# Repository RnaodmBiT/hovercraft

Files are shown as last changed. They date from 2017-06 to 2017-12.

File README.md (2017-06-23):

 # MiniBot

This project will produce a PCB design that can be used for prototyping remote control vehicles. It is inspired by the University of Canterbury ECE Departments 'Wacky Racers' competition. The objective is to follow most of the rules of that competition however the entire design will fit on a single PCB and be as small as possible.

 ## Requirements
  - Support a number of external ESCs and Servos.
  - Be remote controlled. This might require a second USB dongle to be produced if Bluetooth or WiFi isn't used.
  - It should include an accelerometer, gyroscope, and magnetometer for any control systems.
  - Be programmable over SWD or USB.
  - Use as minimum number of parts.
  - Make use of an STM32 microcontroller.
  - Provide external PIO access for use in different projects.

 ## Connectivity
  - Radio
    - RN41
      - UART
      - LED connected to GPIO5 (Open Drain)
      - Connect GPIOs 3/4/6 to GND
      - Connect GPIO 7 to ground with solder bridge high

  - Accelerometer
    - LSM6DS3US
      - I2C

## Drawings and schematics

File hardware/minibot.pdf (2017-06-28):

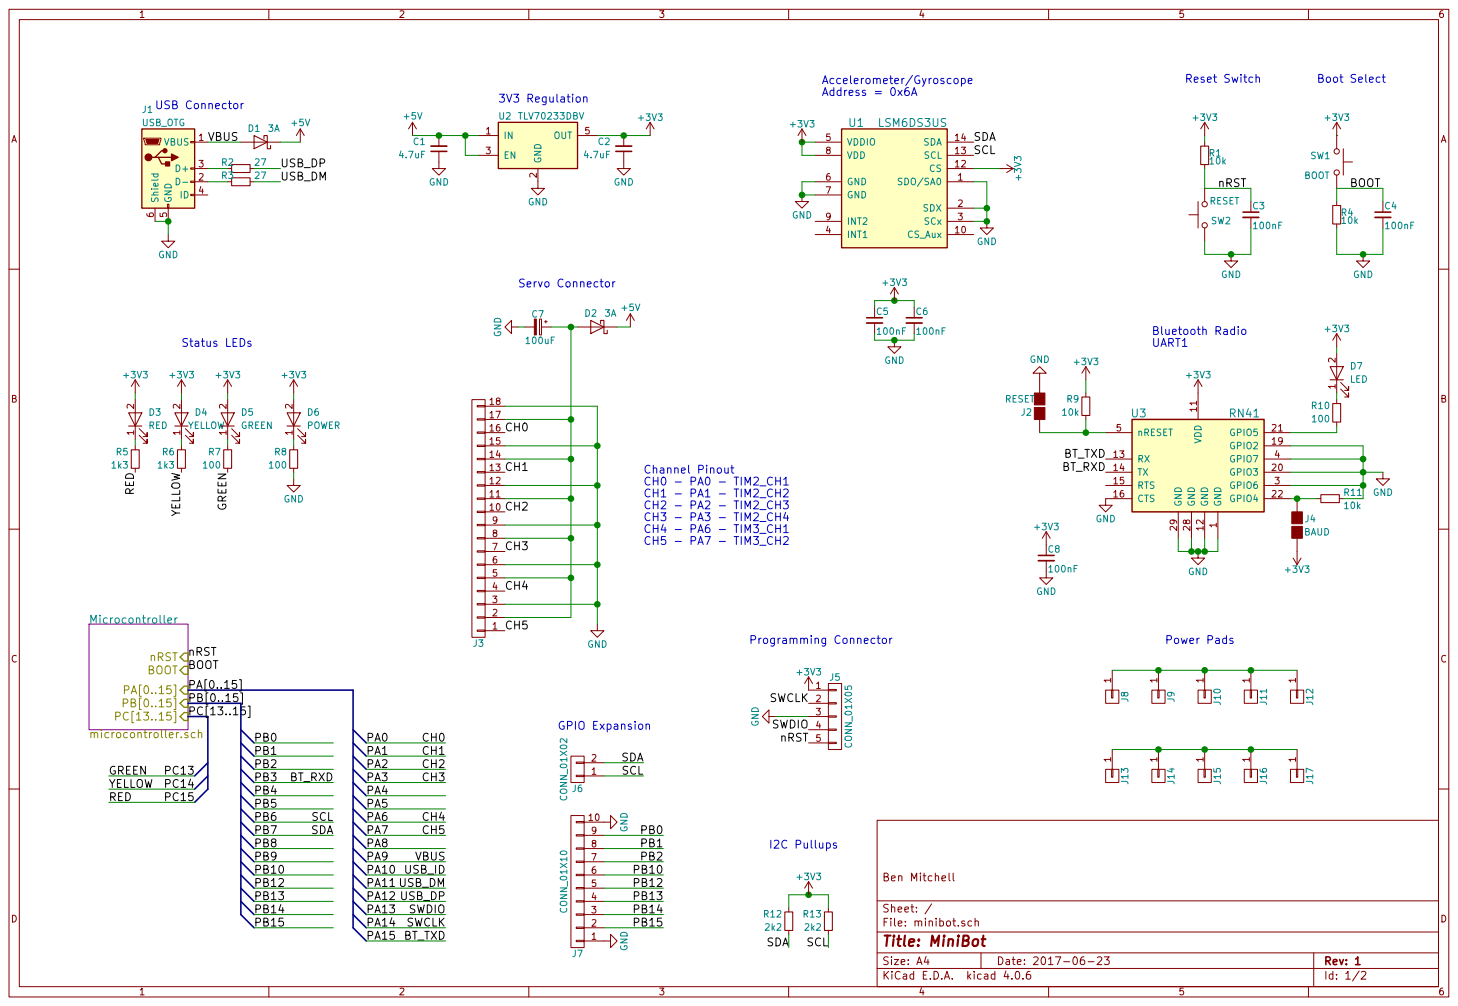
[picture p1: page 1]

17
CH0 15

14
CH1 12

11
CH2 9

CH3 6

CH4 3

Id: 1/2 Title: MiniBot File: minibot.sch Sheet: / Ben Mitchell Microcontroller microcontroller.sch

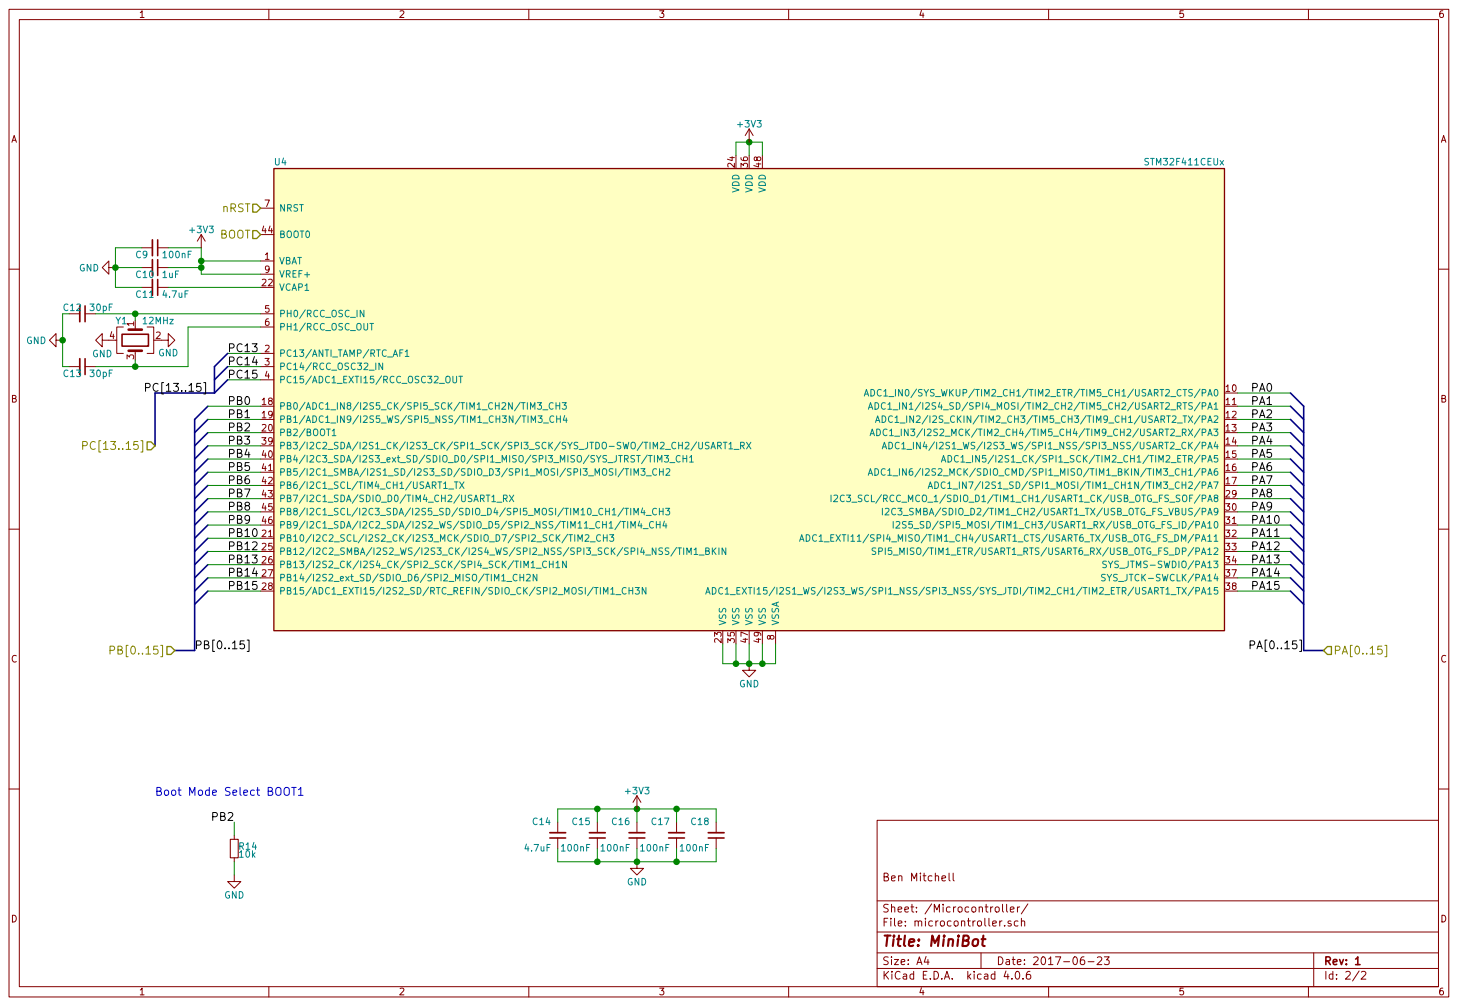
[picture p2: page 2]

Id: 2/2 Title: MiniBot File: microcontroller.sch Sheet: /Microcontroller/ Ben Mitchell

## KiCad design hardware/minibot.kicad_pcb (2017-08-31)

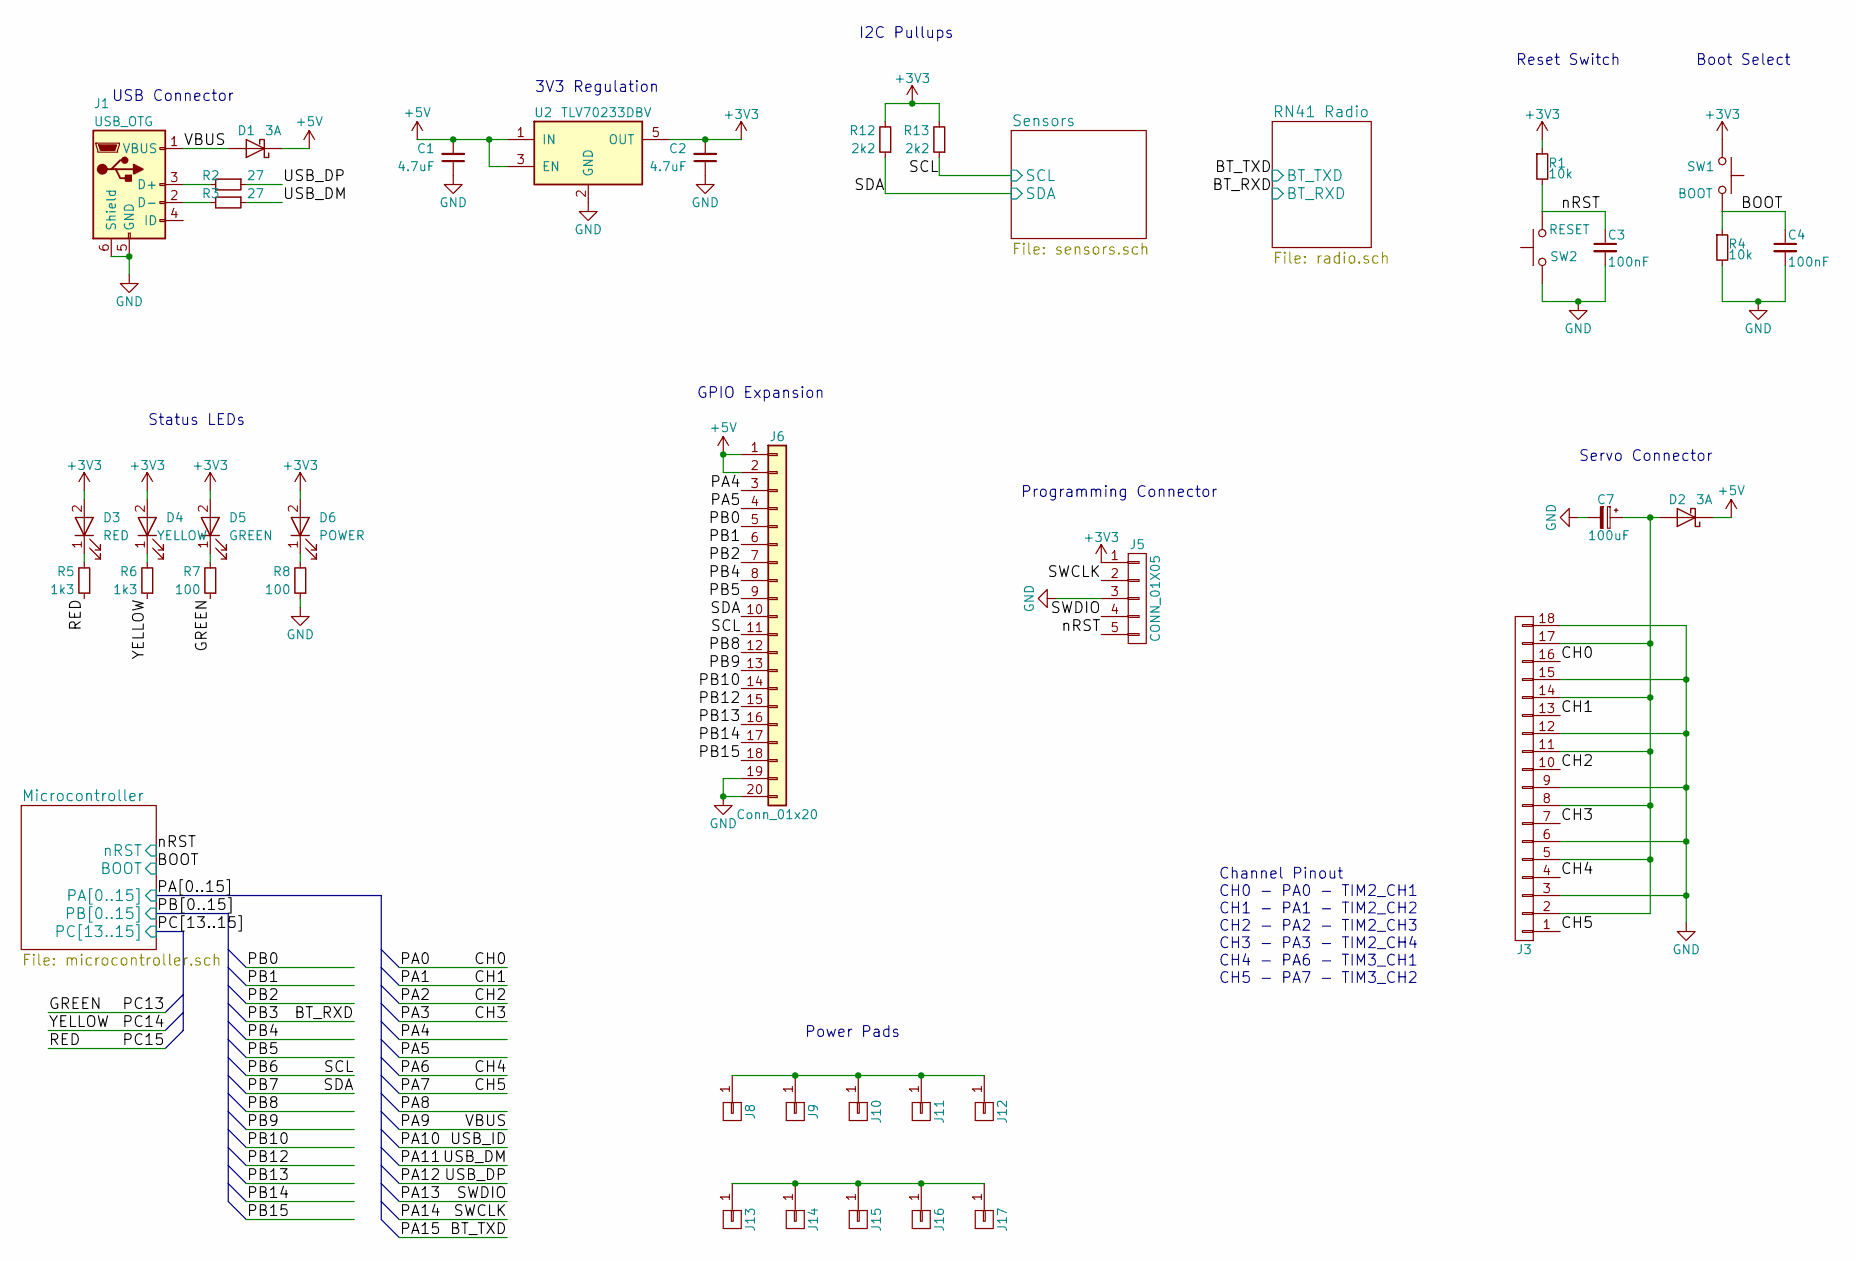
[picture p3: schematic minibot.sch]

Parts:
C1, C2: 4.7uF; C_0805
C3, C4: 100nF; C_0603
C7: 100uF; CP_Elec_6.3x5.3
D1, D2: 3A; D_SMA
D3: RED; LED_0603
D4: YELLOW; LED_0603
D5: GREEN; LED_0603
D6: POWER; LED_0603
J1: USB_OTG; USB_Micro-B
J3: CONN_01X18; Pin_Header_Angled_3x06_Pitch2.54mm
J5: CONN_01X05; Pin_Header_Straight_1x05_Pitch2.54mm
J6: Conn_01x20; IDC_Header_Straight_20pins
J8, J9, J10, J11, J12, J13, J14, J15, J16, J17: CONN_01X01; Pad
R1, R4: 10k; R_0603
R2, R3: 27; R_0603
R5, R6: 1k3; R_0603
R7, R8: 100; R_0603
R12, R13: 2k2; R_0603
SW1: BOOT; Panasonic_EVQPUK_EVQPUB
SW2: RESET; Panasonic_EVQPUK_EVQPUB
U2: TLV70233DBV; SOT-23-5

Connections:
+3V3: C2.2, D3.2 (A), D4.2 (A), D5.2 (A), D6.2 (A), J5.1, R1.1, R12.2, R13.2, SW1.1, U2.5 (OUT); also elsewhere on the board
+5V: C1.2, D1.1 (K), D2.1 (K), J6.1, J6.2, U2.1 (IN), U2.3 (EN)
/BOOT: C4.1, R4.1, SW1.2; also elsewhere on the board
/CH0: J3.16; also elsewhere on the board
/CH1: J3.13; also elsewhere on the board
/CH2: J3.10; also elsewhere on the board
/CH3: J3.7; also elsewhere on the board
/CH4: J3.4; also elsewhere on the board
/CH5: J3.1; also elsewhere on the board
/GREEN: R7.1; also elsewhere on the board
/PA4: J6.3; also elsewhere on the board
/PA5: J6.4; also elsewhere on the board
/PA9: D1.2 (A), J1.1 (VBUS); also elsewhere on the board
/PA11: R3.1; also elsewhere on the board
/PA12: R2.1; also elsewhere on the board
/PA13: J5.4; also elsewhere on the board
/PA14: J5.2; also elsewhere on the board
/PB0: J6.5; also elsewhere on the board
/PB1: J6.6; also elsewhere on the board
/PB2: J6.7; also elsewhere on the board
/PB4: J6.8; also elsewhere on the board
/PB5: J6.9; also elsewhere on the board
/PB6: J6.11, R13.1; also elsewhere on the board
/PB7: J6.10, R12.1; also elsewhere on the board
/PB8: J6.12; also elsewhere on the board
/PB9: J6.13; also elsewhere on the board
/PB10: J6.14; also elsewhere on the board
/PB12: J6.15; also elsewhere on the board
/PB13: J6.16; also elsewhere on the board
/PB14: J6.17; also elsewhere on the board
/PB15: J6.18; also elsewhere on the board
/PC14: R6.1; also elsewhere on the board
/PC15: R5.1; also elsewhere on the board
/nRST: C3.1, J5.5, R1.2, SW2.2; also elsewhere on the board
GND: C1.1, C2.1, C3.2, C4.2, C7.2, J1.5 (GND), J1.6 (Shield), J3.3, J3.6, J3.9, J3.12, J3.15, J3.18, J5.3, J6.19, J6.20, R4.2, R8.1, SW2.1, U2.2 (GND); also elsewhere on the board
unnamed: C7.1, D2.2 (A), J3.2, J3.5, J3.8, J3.11, J3.14, J3.17
unnamed: D3.1 (K), R5.2
unnamed: D4.1 (K), R6.2
unnamed: D5.1 (K), R7.2
unnamed: D6.1 (K), R8.2
unnamed: J1.2 (D-), R3.2
unnamed: J1.3 (D+), R2.2
unnamed: J8.1, J9.1, J10.1, J11.1, J12.1
unnamed: J13.1, J14.1, J15.1, J16.1, J17.1

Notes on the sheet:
Reset Switch
Boot Select
Servo Connector
USB Connector
3V3 Regulation
Status LEDs
Programming Connector
I2C Pullups
Channel Pinout CH0 - PA0 - TIM2_CH1 CH1 - PA1 - TIM2_CH2 CH2 - PA2 - TIM2_CH3 CH3 - PA3 - TIM2_CH4 CH4 - PA6 - TIM3_CH1 CH5 - PA7 - TIM3_CH2
GPIO Expansion
Power Pads

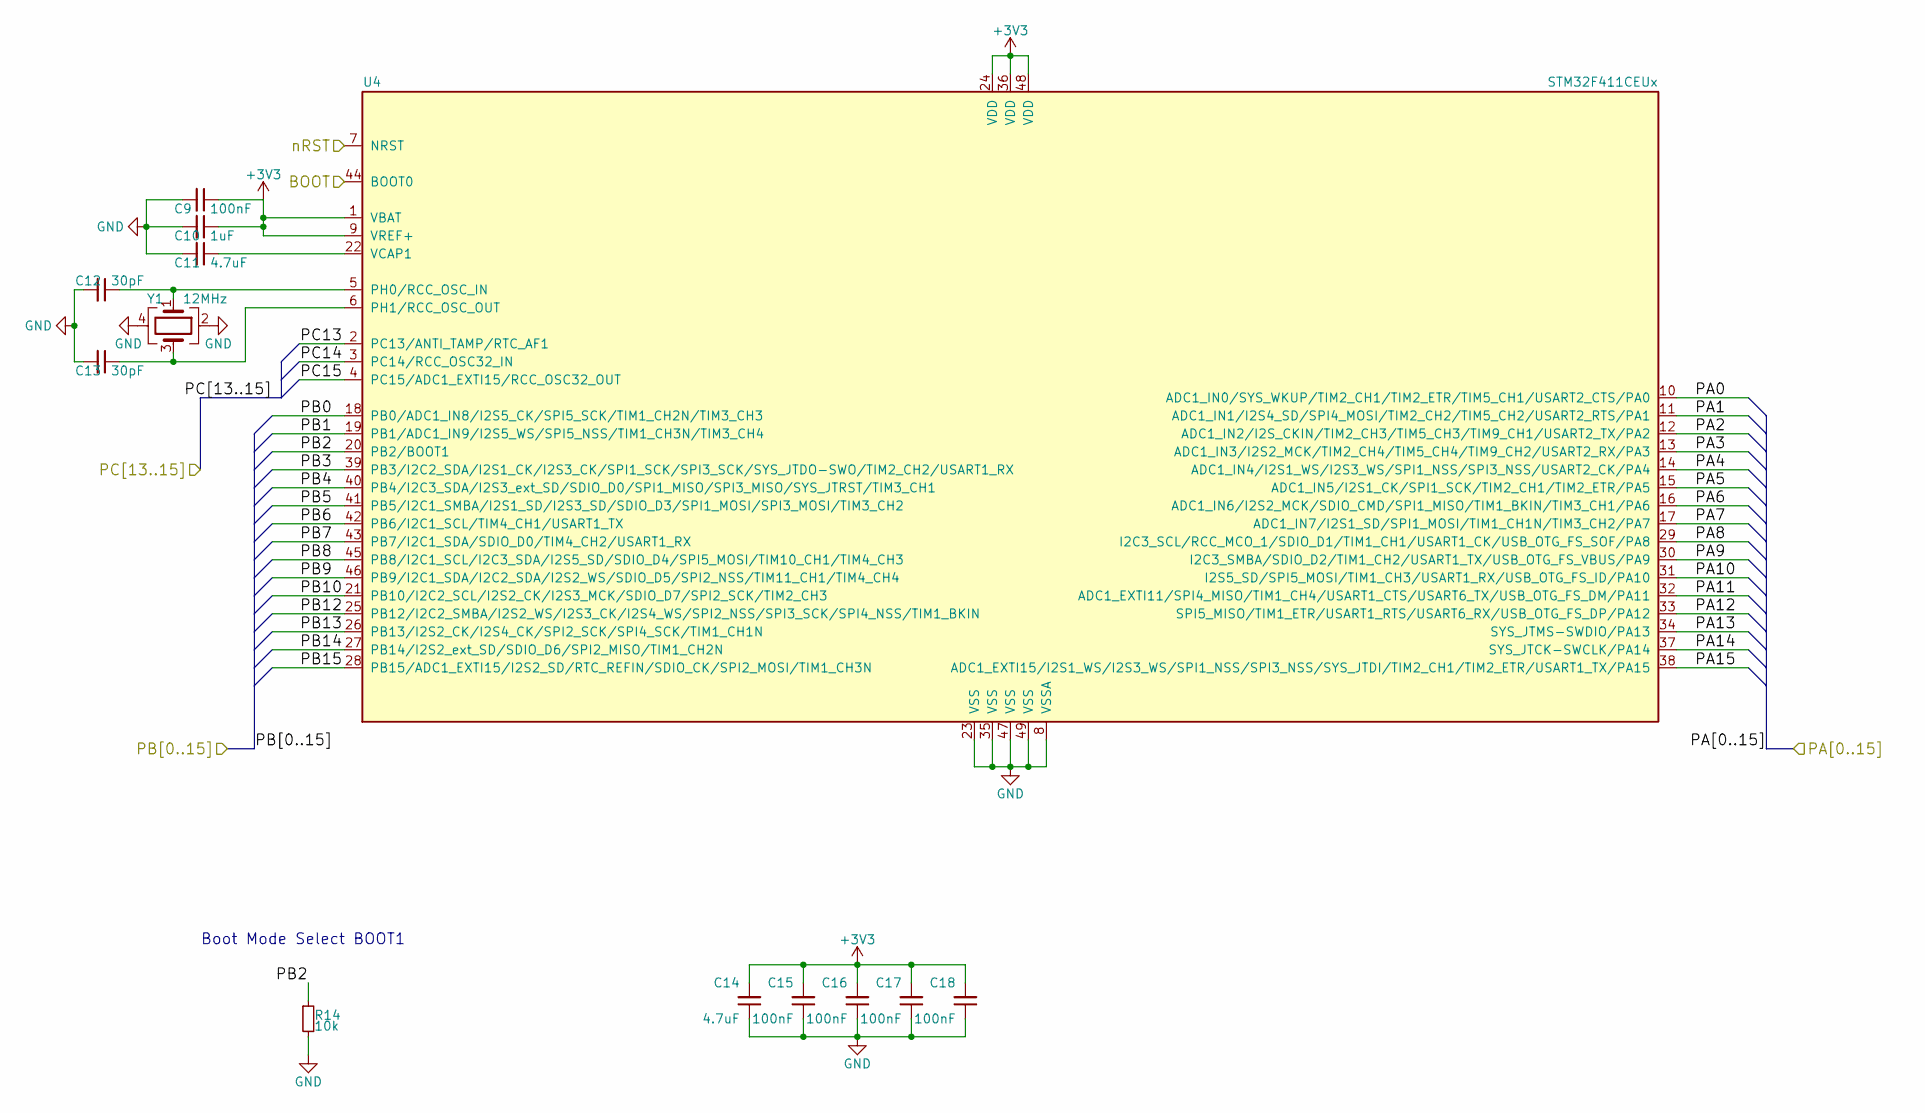
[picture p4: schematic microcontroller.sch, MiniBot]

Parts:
C9, C15, C16, C17, C18: 100nF; C_0603
C10: 1uF; C_0805
C11, C14: 4.7uF; C_0805
C12, C13: 30pF; C_0402
R14: 10k; R_0603
U4: STM32F411CEUx; TQFP-48_7x7mm_Pitch0.5mm
Y1: 12MHz; Crystal_SMD_3225-4pin_3.2x2.5mm

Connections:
+3V3: C9.1, C10.1, C14.2, C15.2, C16.2, C17.2, C18.2, U4.1 (VBAT), U4.9 (VREF+), U4.24 (VDD), U4.36 (VDD), U4.48 (VDD); also elsewhere on the board
/BOOT: U4.44 (BOOT0); also elsewhere on the board
/BT_RXD: U4.39 (PB3/I2C2_SDA/I2S1_CK/I2S3_CK/SPI1_SCK/S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); also elsewhere on the board
/BT_TXD: U4.38 (ADC1_EXTI15/I2S1_WS/I2S3_WS/SPI1_NSS/SP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); also elsewhere on the board
/CH0: U4.10 (ADC1_IN0/SYS_WKUP/TIM2_CH1/TIM2_ETR/TIM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); also elsewhere on the board
/CH1: U4.11 (ADC1_IN1/I2S4_SD/SPI4_MOSI/TIM2_CH2/TIM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); also elsewhere on the board
/CH2: U4.12 (ADC1_IN2/I2S_CKIN/TIM2_CH3/TIM5_CH3/TIM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); also elsewhere on the board
/CH3: U4.13 (ADC1_IN3/I2S2_MCK/TIM2_CH4/TIM5_CH4/TIM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); also elsewhere on the board
/CH4: U4.16 (ADC1_IN6/I2S2_MCK/SDIO_CMD/SPI1_MISO/TI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); also elsewhere on the board
/CH5: U4.17 (ADC1_IN7/I2S1_SD/SPI1_MOSI/TIM1_CH1N/TI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); also elsewhere on the board
/GREEN: U4.2 (PC13/ANTI_TAMP/RTC_AF1); also elsewhere on the board
/PA4: U4.14 (ADC1_IN4/I2S1_WS/I2S3_WS/SPI1_NSS/SPI3_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); also elsewhere on the board
/PA5: U4.15 (ADC1_IN5/I2S1_CK/SPI1_SCK/TIM2_CH1/TIM2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); also elsewhere on the board
/PA8: U4.29 (I2C3_SCL/RCC_MCO_1/SDIO_D1/TIM1_CH1/USA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)
/PA9: U4.30 (I2C3_SMBA/SDIO_D2/TIM1_CH2/USART1_TX/US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); also elsewhere on the board
/PA10: U4.31 (I2S5_SD/SPI5_MOSI/TIM1_CH3/USART1_RX/US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)
/PA11: U4.32 (ADC1_EXTI11/SPI4_MISO/TIM1_CH4/USART1_C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); also elsewhere on the board
/PA12: U4.33 (SPI5_MISO/TIM1_ETR/USART1_RTS/USART6_RX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); also elsewhere on the board
/PA13: U4.34 (SYS_JTMS-SWDIO/PA13); also elsewhere on the board
/PA14: U4.37 (SYS_JTCK-SWCLK/PA14); also elsewhere on the board
/PB0: U4.18 (PB0/ADC1_IN8/I2S5_CK/SPI5_SCK/TIM1_CH2N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); also elsewhere on the board
/PB1: U4.19 (PB1/ADC1_IN9/I2S5_WS/SPI5_NSS/TIM1_CH3N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); also elsewhere on the board
/PB2: R14.1, U4.20 (PB2/BOOT1); also elsewhere on the board
/PB4: U4.40 (PB4/I2C3_SDA/I2S3_ext_SD/SDIO_D0/SPI1_M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); also elsewhere on the board
/PB5: U4.41 (PB5/I2C1_SMBA/I2S1_SD/I2S3_SD/SDIO_D3/S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); also elsewhere on the board
/PB6: U4.42 (PB6/I2C1_SCL/TIM4_CH1/USART1_TX); also elsewhere on the board
/PB7: U4.43 (PB7/I2C1_SDA/SDIO_D0/TIM4_CH2/USART1_RX); also elsewhere on the board
/PB8: U4.45 (PB8/I2C1_SCL/I2C3_SDA/I2S5_SD/SDIO_D4/S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); also elsewhere on the board
/PB9: U4.46 (PB9/I2C1_SDA/I2C2_SDA/I2S2_WS/SDIO_D5/S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); also elsewhere on the board
/PB10: U4.21 (PB10/I2C2_SCL/I2S2_CK/I2S3_MCK/SDIO_D7/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); also elsewhere on the board
/PB12: U4.25 (PB12/I2C2_SMBA/I2S2_WS/I2S3_CK/I2S4_WS/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); also elsewhere on the board
/PB13: U4.26 (PB13/I2S2_CK/I2S4_CK/SPI2_SCK/SPI4_SCK/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); also elsewhere on the board
/PB14: U4.27 (PB14/I2S2_ext_SD/SDIO_D6/SPI2_MISO/TIM1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); also elsewhere on the board
/PB15: U4.28 (PB15/ADC1_EXTI15/I2S2_SD/RTC_REFIN/SDIO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); also elsewhere on the board
/PC14: U4.3 (PC14/RCC_OSC32_IN); also elsewhere on the board
/PC15: U4.4 (PC15/ADC1_EXTI15/RCC_OSC32_OUT); also elsewhere on the board
/nRST: U4.7 (NRST); also elsewhere on the board
GND: C9.2, C10.2, C11.2, C12.2, C13.2, C14.1, C15.1, C16.1, C17.1, C18.1, R14.2, U4.8 (VSSA), U4.23 (VSS), U4.35 (VSS), U4.47 (VSS), U4.49 (VSS), Y1.2, Y1.4; also elsewhere on the board
unnamed: C11.1, U4.22 (VCAP1)
unnamed: C12.1, U4.5 (PH0/RCC_OSC_IN), Y1.1
unnamed: C13.1, U4.6 (PH1/RCC_OSC_OUT), Y1.3

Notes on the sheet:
Boot Mode Select BOOT1

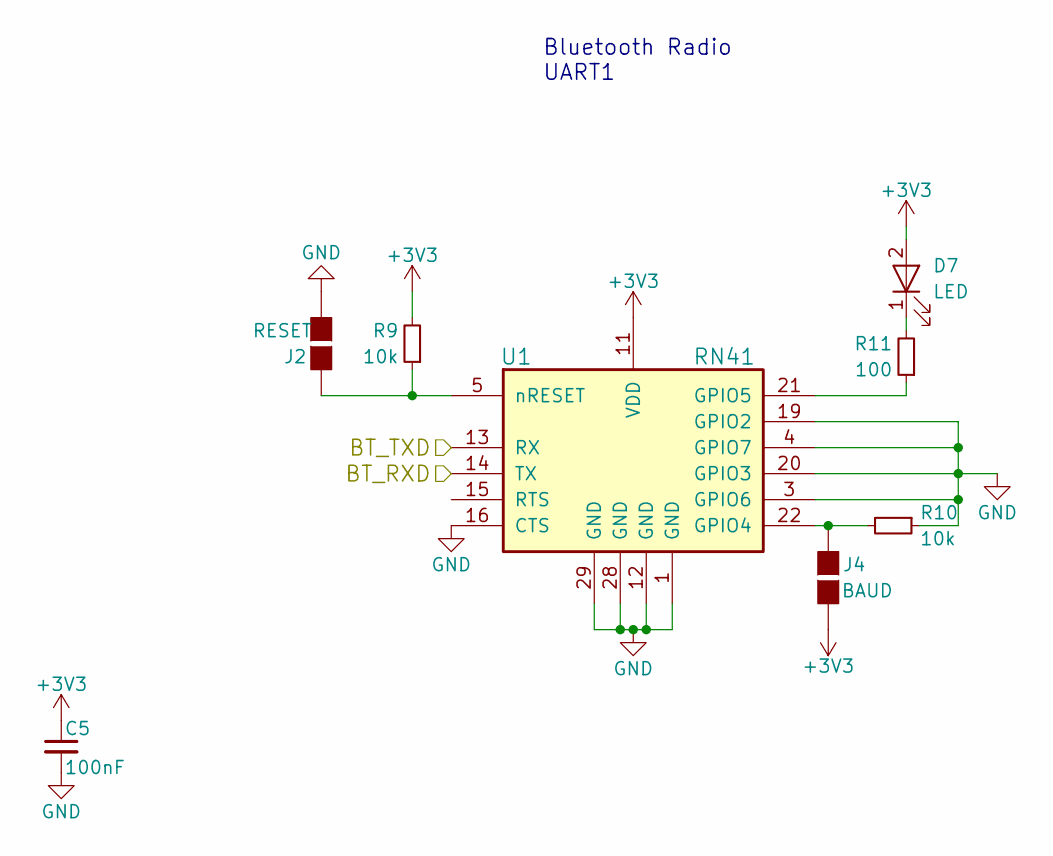
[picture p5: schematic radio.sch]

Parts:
C5: 100nF; C_0603
D7: LED; LED_0603
J2: RESET; GS2
J4: BAUD; GS2
R9, R10: 10k; R_0603
R11: 100; R_0603
U1: RN41

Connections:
+3V3: C5.1, D7.2 (A), J4.2 (G2), R9.2, U1.11 (VDD); also elsewhere on the board
/BT_RXD: U1.14 (TX); also elsewhere on the board
/BT_TXD: U1.13 (RX); also elsewhere on the board
GND: C5.2, J2.2 (G2), R10.1, U1.1 (GND), U1.3 (GPIO6), U1.4 (GPIO7), U1.12 (GND), U1.16 (CTS), U1.19 (GPIO2), U1.20 (GPIO3), U1.28 (GND), U1.29 (GND); also elsewhere on the board
unnamed: D7.1 (K), R11.2
unnamed: J2.1 (G1), R9.1, U1.5 (nRESET)
unnamed: J4.1 (G1), R10.2, U1.22 (GPIO4)
unnamed: R11.1, U1.21 (GPIO5)

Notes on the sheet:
Bluetooth Radio UART1

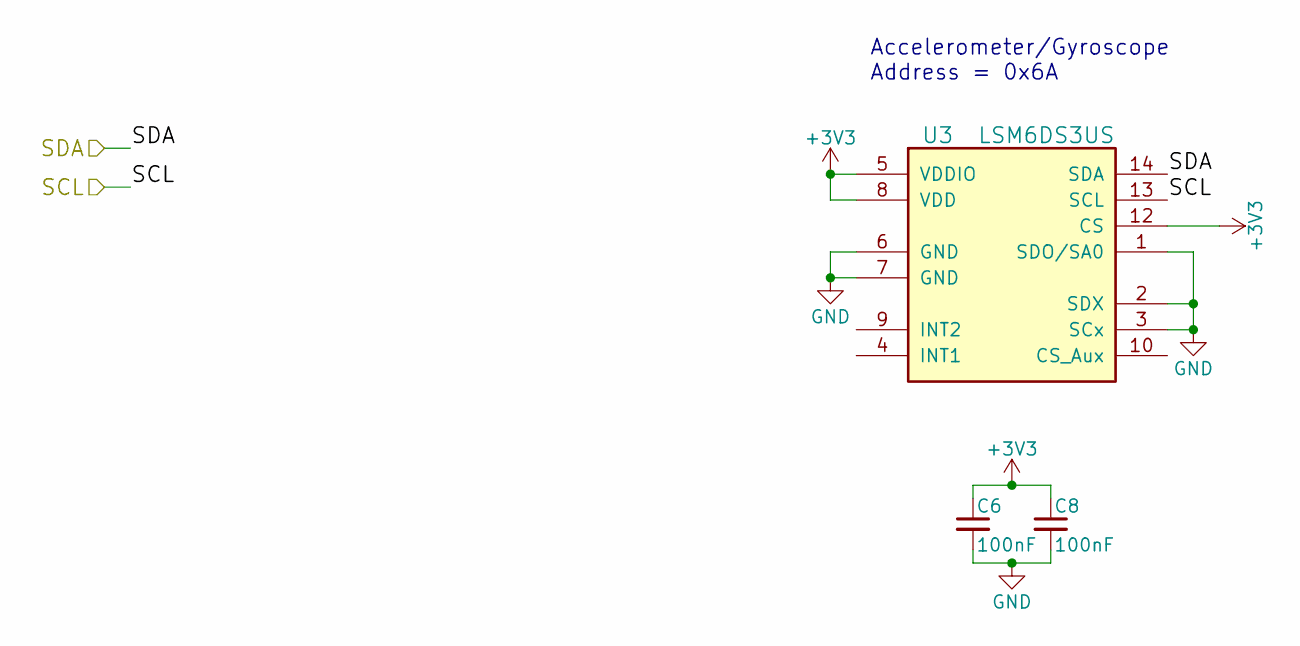
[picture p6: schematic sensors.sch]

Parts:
C6, C8: 100nF; C_0603
U3: LSM6DS3US

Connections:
+3V3: C6.1, C8.1, U3.5 (VDDIO), U3.8 (VDD), U3.12 (CS); also elsewhere on the board
/PB6: U3.13 (SCL); also elsewhere on the board
/PB7: U3.14 (SDA); also elsewhere on the board
GND: C6.2, C8.2, U3.1 (SDO/SA0), U3.2 (SDX), U3.3 (SCx), U3.6 (GND), U3.7 (GND); also elsewhere on the board

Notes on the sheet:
Accelerometer/Gyroscope Address = 0x6A

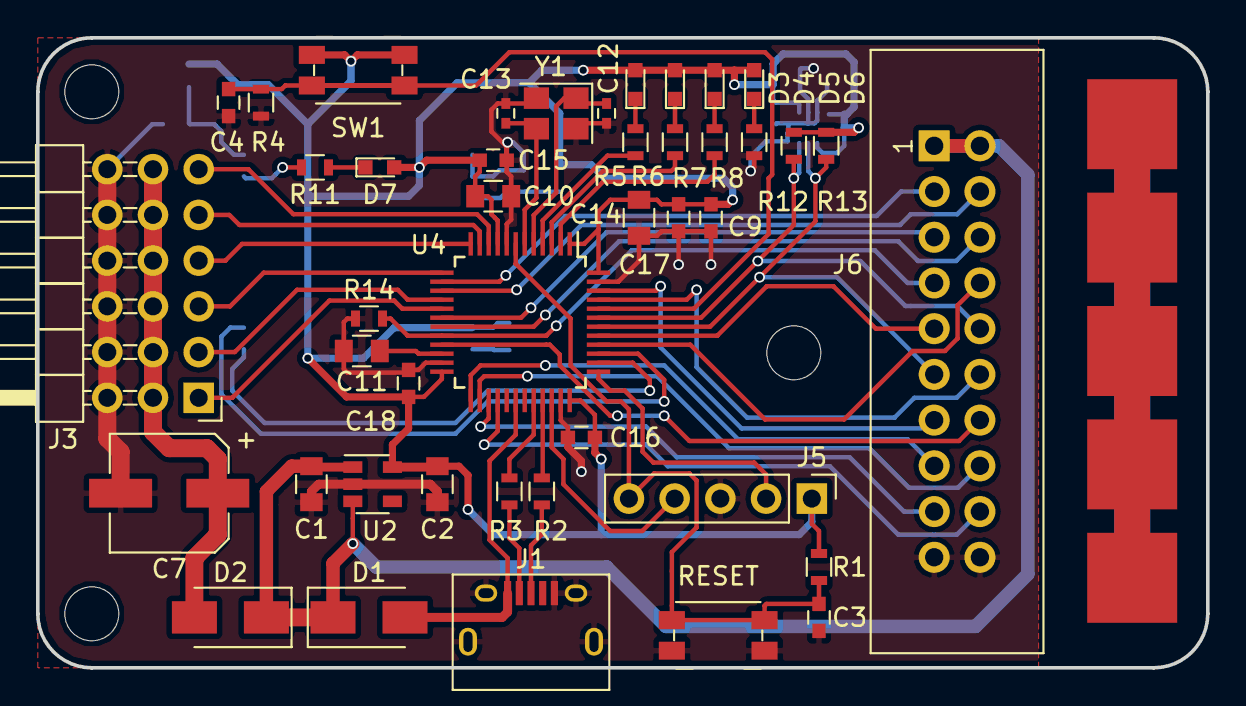
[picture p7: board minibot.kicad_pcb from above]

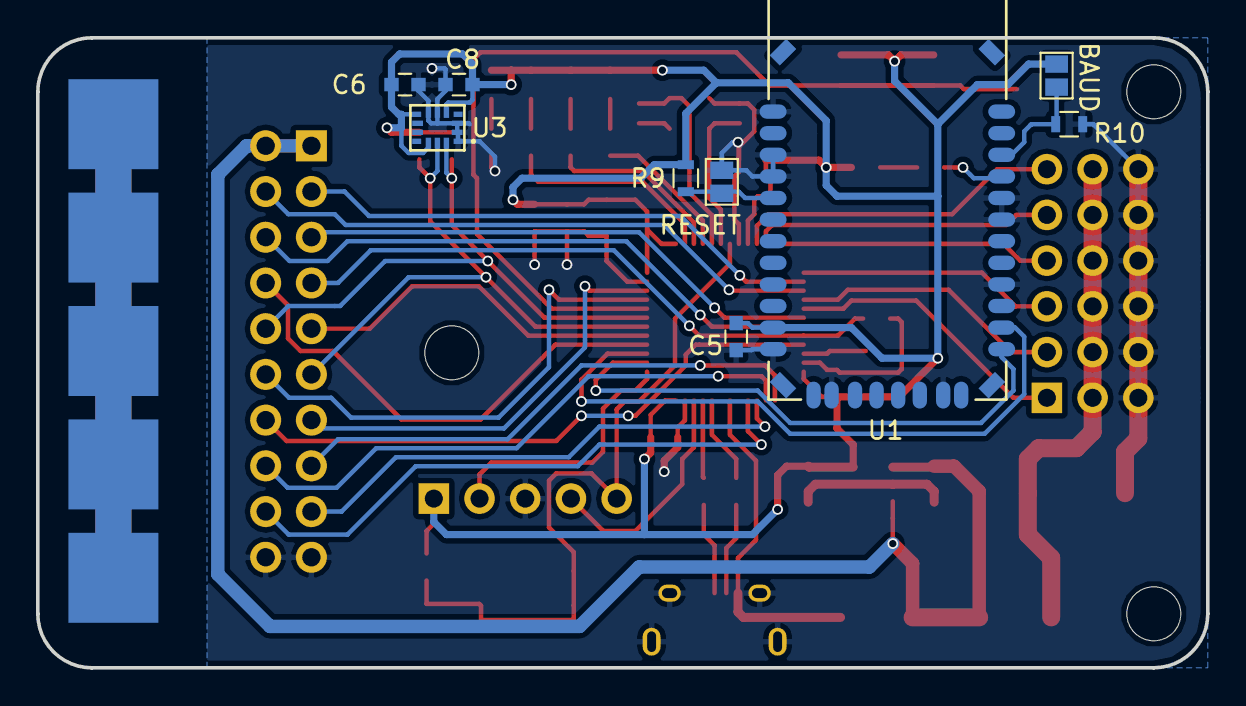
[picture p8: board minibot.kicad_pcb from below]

Board: 2 copper layers, 65.0 x 35.0 mm, 62 parts (14 on the bottom side), 53 nets.

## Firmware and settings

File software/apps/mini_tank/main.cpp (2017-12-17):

#include <stm32f4xx.h>
#include <sys.hpp>
#include <pio.hpp>
#include <pwm.hpp>
#include <uart.hpp>

void SysTickHandler();

static const int SysTickHz = 100000;

static volatile int ticks = 0;

static volatile int timeout = 0;

// Define the status LEDs
Pio green(Pio::C, 13, Pio::Output);
Pio yellow(Pio::C, 14, Pio::Output);
Pio red(Pio::C, 15, Pio::Output);

// Define the left and right motors
Pwm left_led(Pio::C, 15, 100, 100);
Pwm right_led(Pio::C, 13, 100, 100);

Pwm left(Pio::A, 0, 100, 100);
Pwm right(Pio::A, 1, 100, 100);


void main() {
    // Initialize the system
    System::Clock::InitSysTick(SysTickHz, SysTickHandler);
    Pwm::Initialize(SysTickHz);
    Uart::Initialize();

    // Turn off the status LEDs
    green = yellow = red = true;

    int x = 0, y = 0;


    while (1) {
        if (timeout == 0) {
            x = y = 0;
        }

        if (Uart::HasData()) {
            if (Uart::Read() == 74) {
                x = (int)Uart::Read() - 127;
                y = (int)Uart::Read() - 127;
                timeout = SysTickHz / 5;
            }
        }

        int l = ((-y + x) * 100) / 127;
        int r = ((-y - x) * 100) / 127;

        if (l > 100) {
            l = 100;
        }
        if (l < 0) {
            l = 0;
        }

        if (r > 100) {
            r = 100;
        }
        if (r < 0) {
            r = 0;
        }


        left.SetServo(l);
        right.SetServo(r);

        // Used as a visual output of what *should* be happening
        left_led.SetDuty(1000 - 10 * l);
        right_led.SetDuty(1000 - 10 * r);
    }
}


void SysTickHandler() {
    ++ticks;
    Pwm::Update();

    if (timeout > 0) {
        timeout--;
    }
}

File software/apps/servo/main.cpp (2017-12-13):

#include <stm32f4xx.h>
#include <sys.hpp>
#include <pio.hpp>
#include <pwm.hpp>

void SysTickHandler();

static const int SysTickHz = 100000;

static volatile int ticks = 0;

// Define the status LEDs
Pio green(Pio::C, 13, Pio::Output);
Pio yellow(Pio::C, 14, Pio::Output);
Pio red(Pio::C, 15, Pio::Output);


void main() {
    System::Clock::InitSysTick(SysTickHz, SysTickHandler);
    Pwm::Initialize(SysTickHz);

    // Channel 0 will be used to control a servo at 100 Hz
    Pwm ch0(Pio::A, 0, 100, 100);

    green = false;
    yellow = red = true;

    uint32_t progress = 0;

    while (1) {
        System::DelayMs(10);

        ch0.SetServo(progress++ % 100);
    }
}


void SysTickHandler() {
    ++ticks;

    Pwm::Update();
}

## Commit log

2017-06-09 Add initial PCB design with the ATMEGA32U2 and USB power
    [hovercraft.kicad_pcb, hovercraft.sch]
2017-06-09 Finish the basic layout of the micro. Next the power needs to be sorted and how the micro will talk to the motors
    [hovercraft.kicad_pcb]
2017-06-11 Filled out the schematic with servo and power connectors and populated these on the PCB
    [hovercraft.kicad_pcb, hovercraft.sch]
2017-06-11 Add the HC-12 serial radio module to the component library
    [hovercraft.sch]
2017-06-11 Add the HC-12 foot print and repopulate the board to fit it in.
    [hovercraft.kicad_pcb, hovercraft.sch]
2017-06-11 Added the board dimensions to the layout
    [hovercraft.kicad_pcb]
2017-06-11 Increased some trace thicknesses around the servo connections to reduce thermal buildup
    [hovercraft.kicad_pcb]
2017-06-12 Separated some traces to try reduce crosstalk. Also added a name and version number to the board
    [hovercraft.kicad_pcb]
2017-06-12 Extend the board size to a more natural number and add mounting holes
    [hovercraft.kicad_pcb]
2017-06-13 Moved the servo PWM signals to different pins to free up the SPI for a gyroscope/accelerometer/magnetometer
    [hovercraft.kicad_pcb, hovercraft.sch]
2017-06-13 Tidied up the file structure
    [minibot.kicad_pcb, minibot.sch]
2017-06-13 Plot a PDF of the schematic
2017-06-13 Add decoupling to the micro, radio, and USB power
    [minibot.sch]
2017-06-13 Update the schematic PDF
2017-06-14 Upgrade the specifications and wipe the previous attempt as we will need to start again.
    [minibot.kicad_pcb, minibot.sch]
2017-06-14 Added a simple STM32 schematic. This includes power, clock, and busses for the GPIO
    [minibot.kicad_pcb, minibot.sch]
2017-06-15 Moved the microcontroller to another sheet and setup the boot and reset switches
    [microcontroller.sch, minibot.sch]
2017-06-15 Add the RN41 radio and a header for the servos
    [microcontroller.sch, minibot.sch]
2017-06-15 Add a USB connector and 3.3V regulation
    [minibot.sch]
2017-06-15 Broke out the A and B PIO ports. Added status LEDs
    [minibot.sch]
2017-06-15 Fix the PORT A numbering. Add the ST Link JTAG connector
    [microcontroller.sch, minibot.sch]
2017-06-16 Change the JTAG connector to an SWD connector. Also start connecting the MCU pins in a clear and visible manner
    [minibot.sch]
2017-06-16 Plotted the schematic
2017-06-16 Map the servo channels. Wire up the BT USART. Add an IMU and an I2C bus. Update the schematic PDF.
    [microcontroller.sch, minibot.sch]
2017-06-16 Add missing decoupling capacitor to the RN41
    [minibot.sch]
2017-06-16 Map all of the inputs except for the debugging LEDs. Still need to work out how to deal with the camera.
    [minibot.sch]
2017-06-18 Add the camera and finish off the schematic.
    [microcontroller.sch, minibot.sch]
2017-06-18 Fix the servo channels to ensure they use different PWM outputs. This required removing the flow control from the RN41 so CTS was tied to ground.
    [minibot.sch]
2017-06-18 Add missing camera decoupling. Annotate all parts.
    [microcontroller.sch, minibot.sch]
2017-06-18 Associate the simple parts with footprints. Some custom footprints will need to be designed.
    [microcontroller.sch, minibot.sch]
2017-06-19 Add in some logic level translation for the camera signals. Update the annotations and plot the PDF
    [microcontroller.sch, minibot.sch]
2017-06-23 Remove the camera from the schematic as it's no longer a reasonable goal
    [minibot.sch]
2017-06-23 Start adjusting the signals now that the camera isn't in the way
    [minibot.sch]
2017-06-23 Start laying out the components for the PCB
    [microcontroller.sch, minibot.kicad_pcb, minibot.sch]
2017-06-26 Modify the schematic and PCB. At this stage the pinout should be considered and very careful selection of which peripheral goes where needs to be done.
    [microcontroller.sch, minibot.kicad_pcb, minibot.sch]
2017-06-27 Redo the pinout. Plot the PDF. Layout the rest of the board.
    [microcontroller.sch, minibot.kicad_pcb, minibot.sch]
2017-06-28 Tweak the layout a little bit. Add mounting holes and some pads to solder the power leads onto.
    [minibot.kicad_pcb, minibot.sch]
2017-06-28 Plot the latest schematic
    [minibot.sch]
2017-06-28 Move a trace to reduce crosstalk.
    [minibot.kicad_pcb]
2017-06-29 Fix the USB overlapping with the RN41
    [minibot.kicad_pcb, minibot.sch]
2017-08-28 Move the radio, and the sensors to new schematic sheets.
    [camera.sch, microcontroller.sch, minibot.sch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]
2017-08-30 Layed board out for the third time. Doesn't include power traces yet.
    [camera.sch, microcontroller.sch, minibot.kicad_pcb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]
2017-08-31 Finish routing the board again
    [minibot.kicad_pcb]
2017-09-21 Add the gerber files
    [minibot-B.Cu.gbl, minibot-B.Mask.gbs, minibot-B.Paste.gbp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]
2017-09-22 Program the STM32F410CB
2017-09-22 Tidy up the build chain
2017-09-23 Moved the initialised constants into flash memory for now. This needs to be fixed by doing a copy into SRAM to speed things up.
    [main.c]
2017-09-23 Move the vector table and reset_handler into a sys moule. Use this to also setup the external crystal properly. Add a couple of vauge timing functions
    [main.c]
2017-09-25 Add UART to the software. The minibot can now send 'hello world' over BT. Add the two programming manuals to the documents. Also fix the system clock
    [main.c, uart.c]
2017-09-27 Add uart echo program. Start building python interface. Add GDB and OpenOCD support with the STLinkV2
2017-09-28 Started moving the code base into C++. The Pio class is wonderful. Thought should be taken as to how sys and uart will look. The LEDs also flash REALLY fast now, this needs to be debugged
2017-09-29 Fix the linker script to include static data properly. Tweak the build script wrt peripherals. Test rudimentary SysTick code
    [main.cpp, pio.cpp]
2017-09-29 Get the clock running properly at 100 MHz and fix the delay functions.
    [main.cpp]
2017-09-29 Updated the UART apps to the new C++ style. Fix the clocks for the UART, everything is awesome now. It just needs to be classed up
    [main.cpp, pio.cpp, uart.c]
2017-09-30 Update the uart driver to C++. Update uart1 to match
2017-09-30 Update uart_echo to c++ code
2017-11-01 Add an IGBT driver program for the Groundwater project
2017-12-13 Add software PWM support.
2017-12-13 Added a helper function for dealing with servos
